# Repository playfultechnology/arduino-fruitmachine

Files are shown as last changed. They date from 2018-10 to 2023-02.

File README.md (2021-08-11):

# arduino-fruitmachine
This repository contains code listings, wiring diagrams, notes, and other reference information relating to my experiences of disassembling old (generally broken, sold as "for spares for repairs") fruit machines (or, "slot machines", for U.S. friends) into their various constituent components, and then rebuilding their functionality using an Arduino microprocessor as a controller.
Accompanying videos can be found at https://www.youtube.com/playlist?list=PLogiUurtMYtRenE8BooiE4FDIyxuIyZQj

As of July 2021, I have now followed this process with five different machines of different eras and manufacturers (Bell Fruit "Snakes and Ladders", Electrocoin "Magic 100", "Max-a-Million", Global "Tuppenny Nudger" and Global "Phoenix Knights"). Each machine has had different components, features, and designs, and I've tried to update the notes below to cover the different variations I've found.

<!-- ![Fruit Machine](FruitMachine.png?raw=true "Fruit Machine") -->
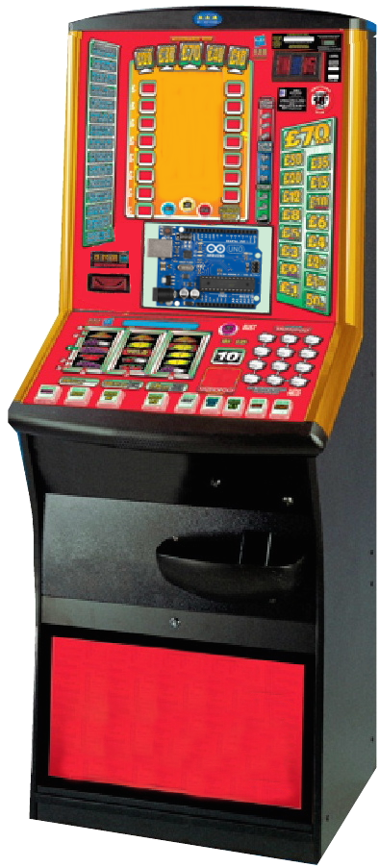
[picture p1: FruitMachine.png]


## Feature Reel
The feature reel is a single standalone reel, which makes it slightly easier to reverse-engineer than the main reels, which typically occur in a connected bank of three or four. It consists of a stepper motor, lamps, and an opto-sensor. Stepper motors may be 12V (in which they can be driven by a4988, DRV8825 stepper motor drivers of a CNC shield) or 24V (in which case they might need an L293D motor driver shield, as shown below)  
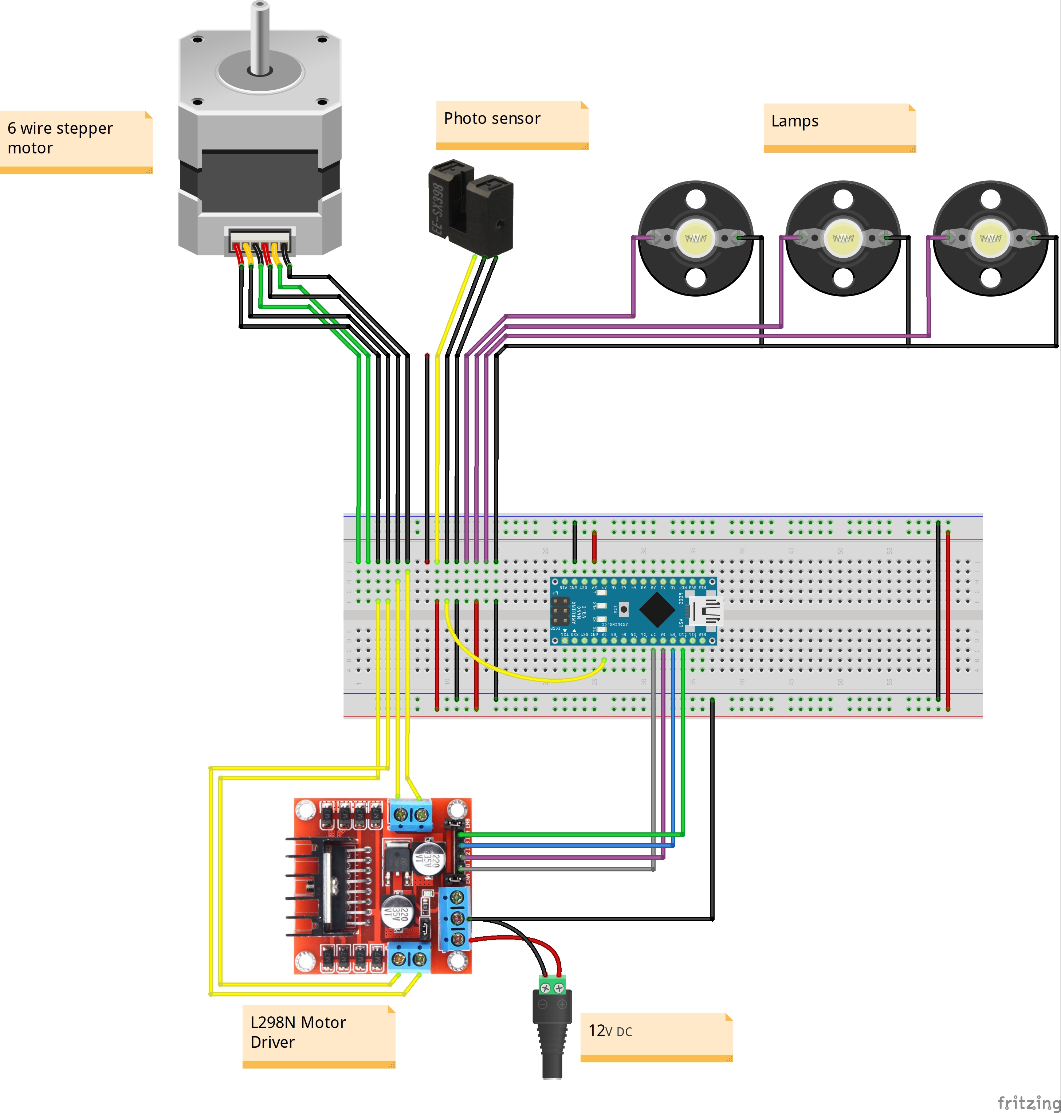
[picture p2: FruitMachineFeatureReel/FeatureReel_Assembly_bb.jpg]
Fruit Machine Feature Reel Fruit Machine Reel Assembly


## Reels
The reels work the same way as the feature reel, except that each has 16 positions, three lamps, and an opto-sensor. Rather than directly wire to a motor driver, I used a RAMPS shield, which provides a convenient way to interface with stepper motor drivers (A4988, DRV8825, TMC2209 or similar)
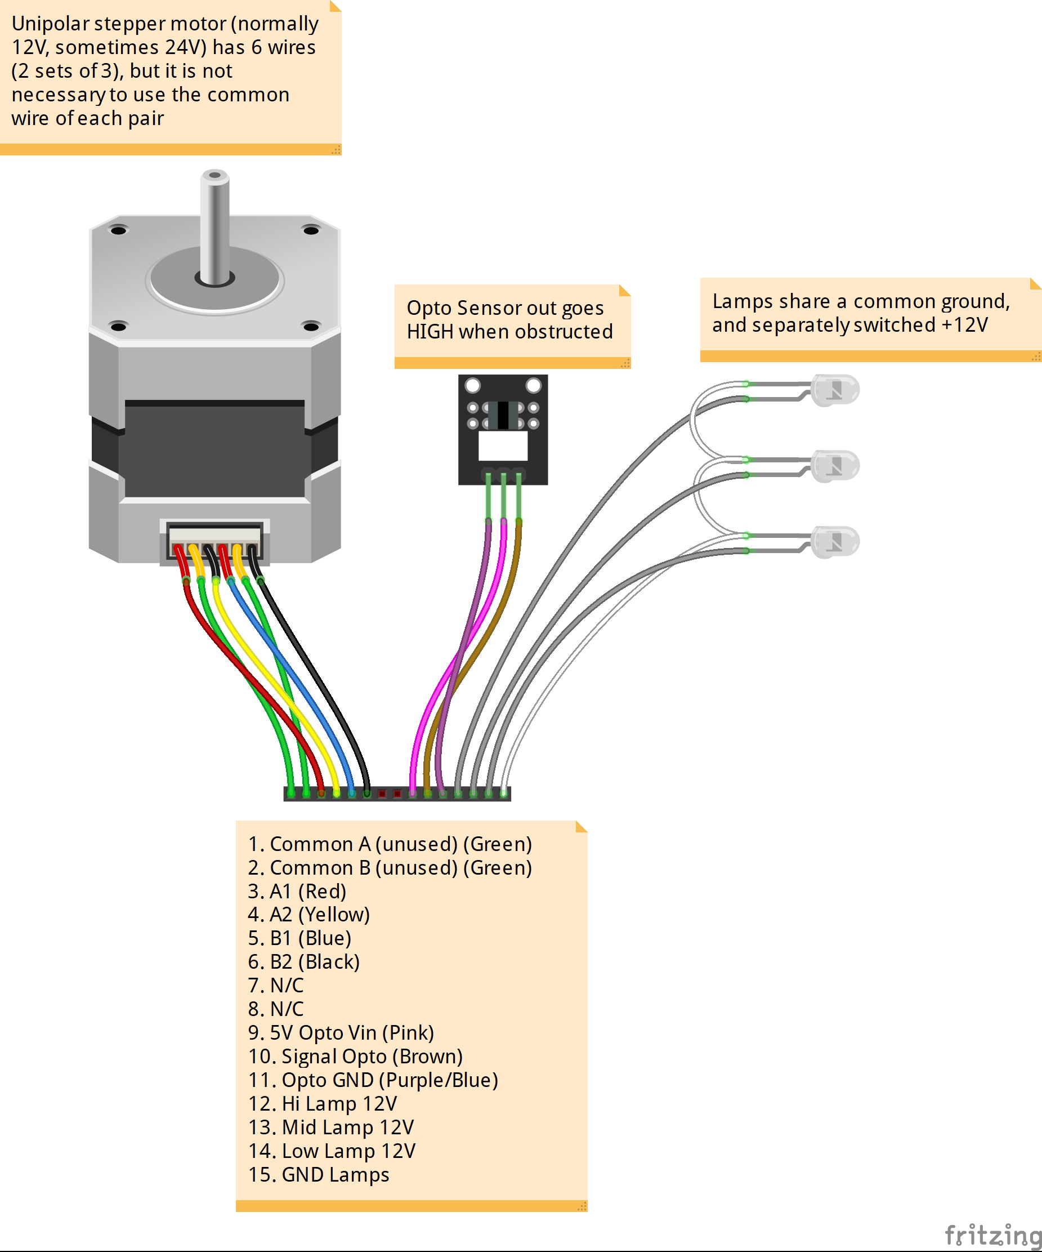
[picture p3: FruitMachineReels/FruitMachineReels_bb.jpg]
Fruit Machine Feature Reel Fruit Machine Reels


## Optosensors (A.K.A. Photosensors, Slotted Optical Switches etc.)
These are the little devices that are used to detect the position of the reels - they consist of a IR transmitter pointing at an IR receiver, with a small gap between them (~1cm). The reels have a small tab protuding from them at one point, which blocks the IR beam as it passes the gap in the sensor, making it possible to know the rotation of the reel at that point. I have encountered several variations of adaptor board which attach the opto-sensors to the reel assmebly, as follows:
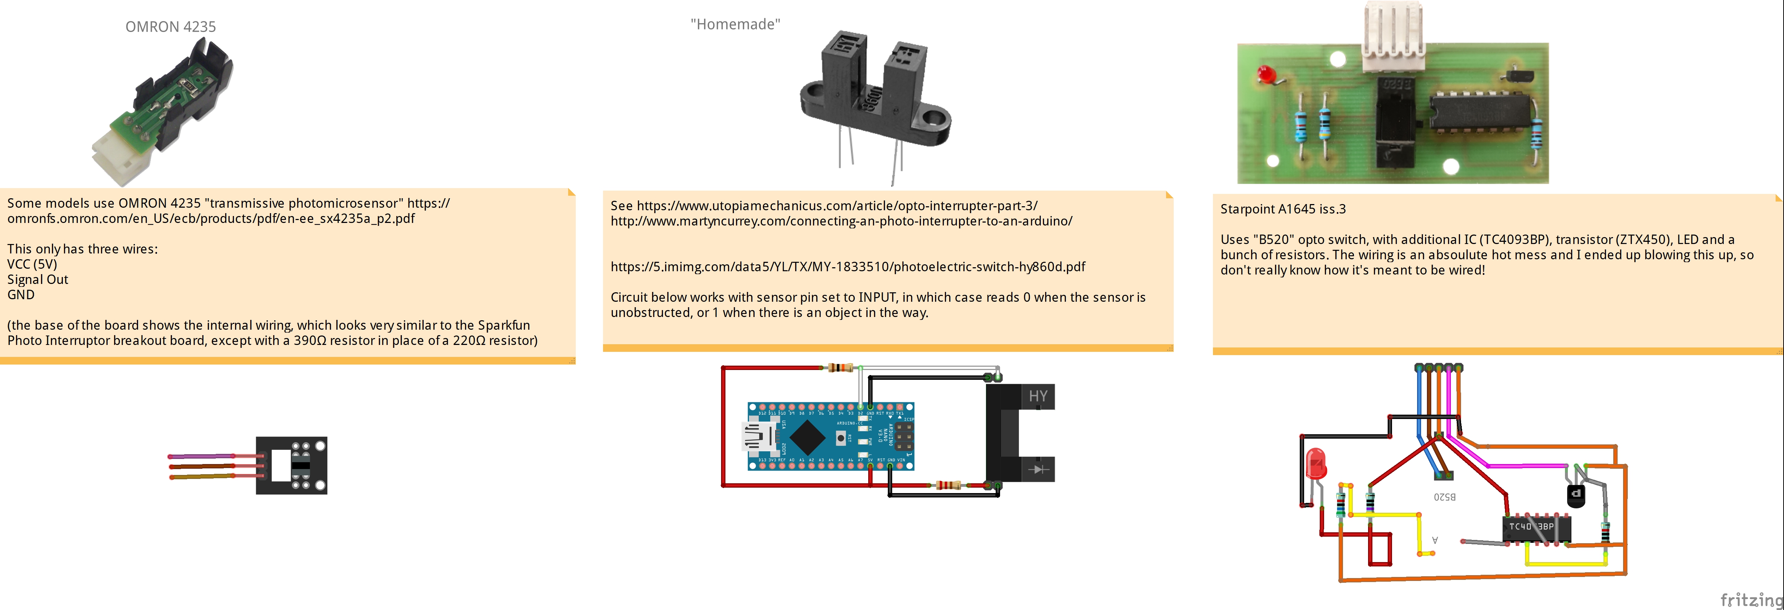
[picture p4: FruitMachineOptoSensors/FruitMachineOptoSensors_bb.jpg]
Fruit Machine Opto Sensors


## Hopper
There are two commonly-used interfaces for coin hoppers - serial and parallel. 
### Parallel interface
The parallel interface is easy to understand - the hopper simply dispenses coins as soon as, and far as long as, 24V power is connected. A coin counter output pin is connected to ground every time a coin exits the hopper, which can be used to cut power once sufficient coins have been dispensed.
### Serial interface
A serial interface called CCTalk was introduced to make universal communication standard with various monetary devices in machines - note validators, coin mechs, and hoppers. The CCTalk standard defines a set of messages that are sent over a serial connection (you can view the documentation here: http://www.coinoperatorshop.com/media/products/manual/cctalk/cctalk44-2.pdf).

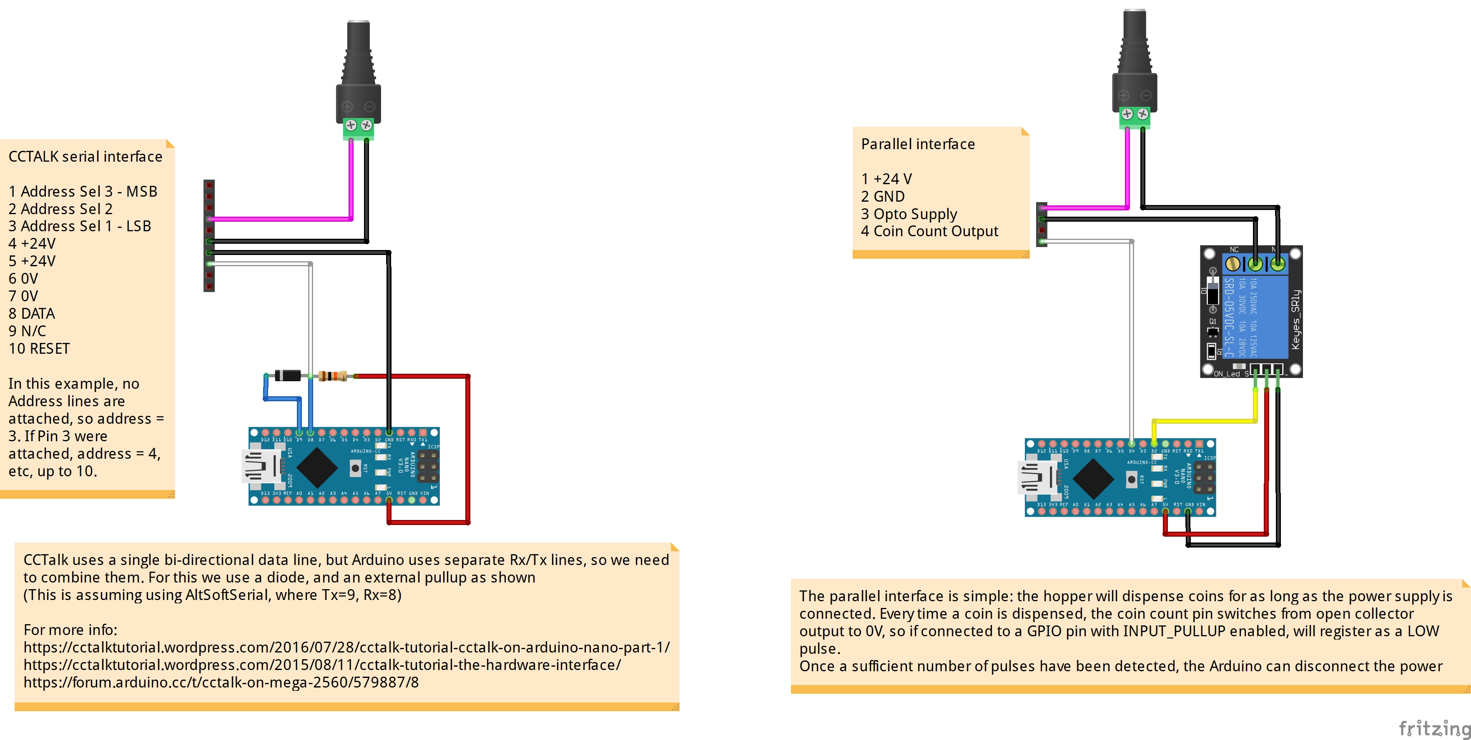
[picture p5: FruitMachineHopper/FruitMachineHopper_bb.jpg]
Fruit Machine Hopper


## LED Display
The primary LED display is formed from five interlocking 1.8" common cathode 7-segment LED displays - datasheet can be found at  http://www.farnell.com/datasheets/99300.pdf
To use the displays, I'm sourcing current into the anodes of each segment using a UDN2981 high-side darlington transistor array (the channels of the UDN2981, corresponding to the segments to be lit, are set by a 74HC595 shift register). The segments of all the displays are wired together, and the particular digit to be lit is selected by grounding the common cathode of that digit through a ULN2803 low-side darlington transistor array. The ULN2803 too is set by a 74HC595 which is daisy-chained to the first, meaning all 5 digit displays can be set using just three pins on the Arduino.

Update: 
 - the 74HC595+UDN2981 on the high side can be replaced with a single MIC5891 8-channel source driver
 - the 74HC595+ULN2803 on the low side can be replaced with a single TPIC6595 8-channel sink driver

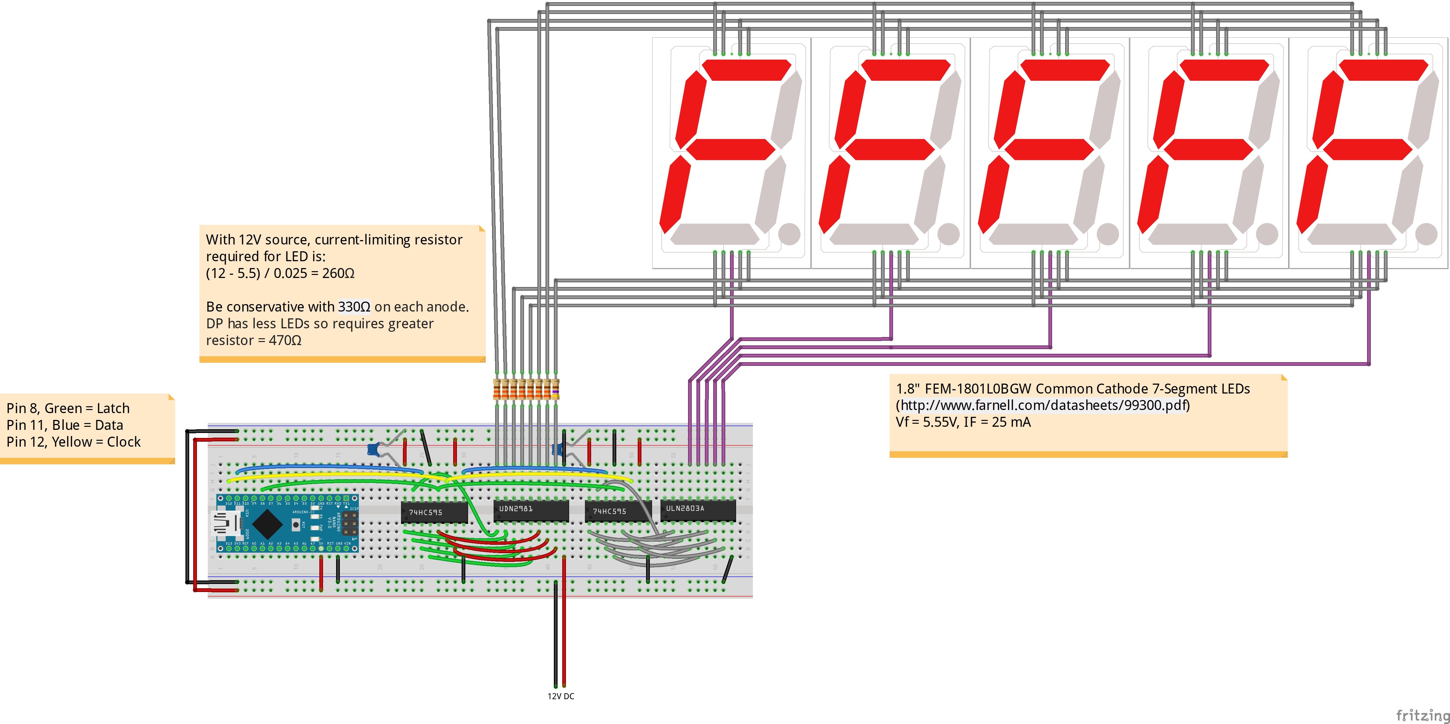
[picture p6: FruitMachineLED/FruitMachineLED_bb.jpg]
Fruit Machine LED Displays Fruit Machine LED Display


## VFD Display
https://picaxeforum.co.uk/threads/using-spi-serial-vfds-from-fruit-machines-with-picaxe-comprehensive-code-examples.22552/
https://www.fruitemu.co.uk/ib/index.php?app=forums&module=forums&controller=topic&id=17419

## Lamps
The incandescent lamps were arranged into groups around the machine, attached to long harnesses consisting of cable-tied wires, rather resembling a spinal column. 
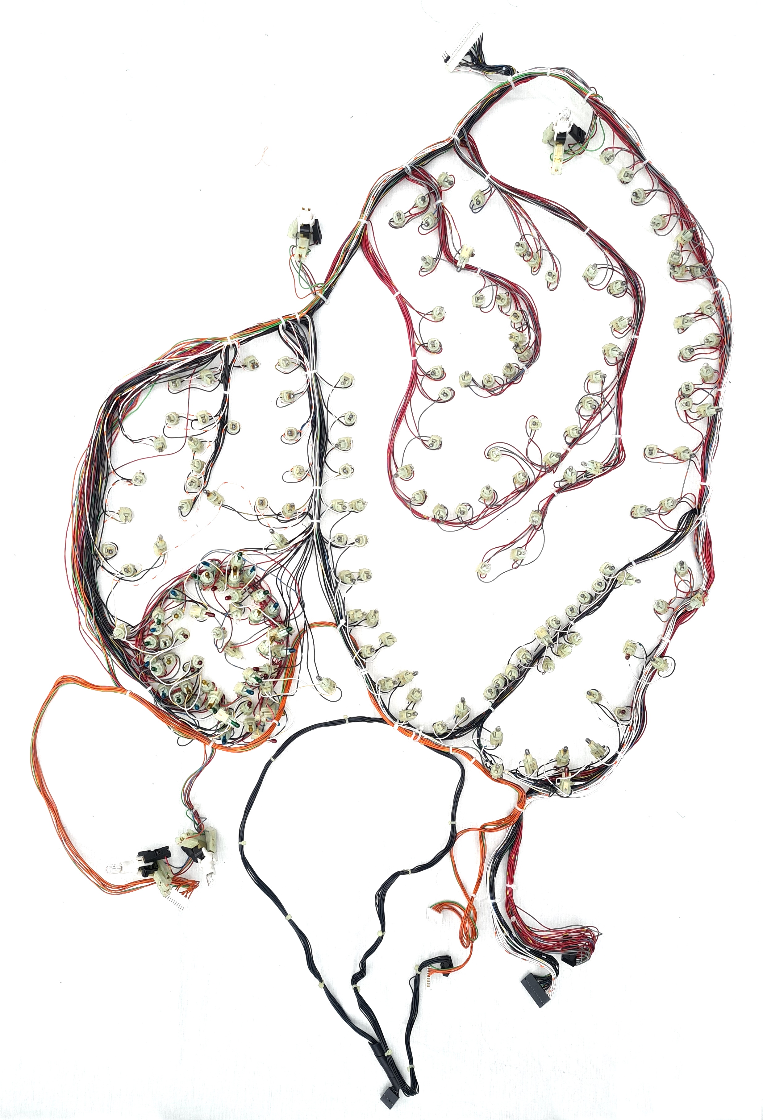
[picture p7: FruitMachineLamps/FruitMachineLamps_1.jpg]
Fruit Machine Lamp Wiring


Although the lamps themselves do not have polarity, the bulb holders typically have had a small inline diode inserted the housing, meaning they have a distinct "positive" and "negative" side. As such, wiring them is much the same as wiring 12V LEDs. Note that the colouring of the wires does not necessarily follow any standard convention: in the following photograph, note the line signifying the cathode of the diode shows the *red* wire is GND, while the *grey* wire is +12V.  
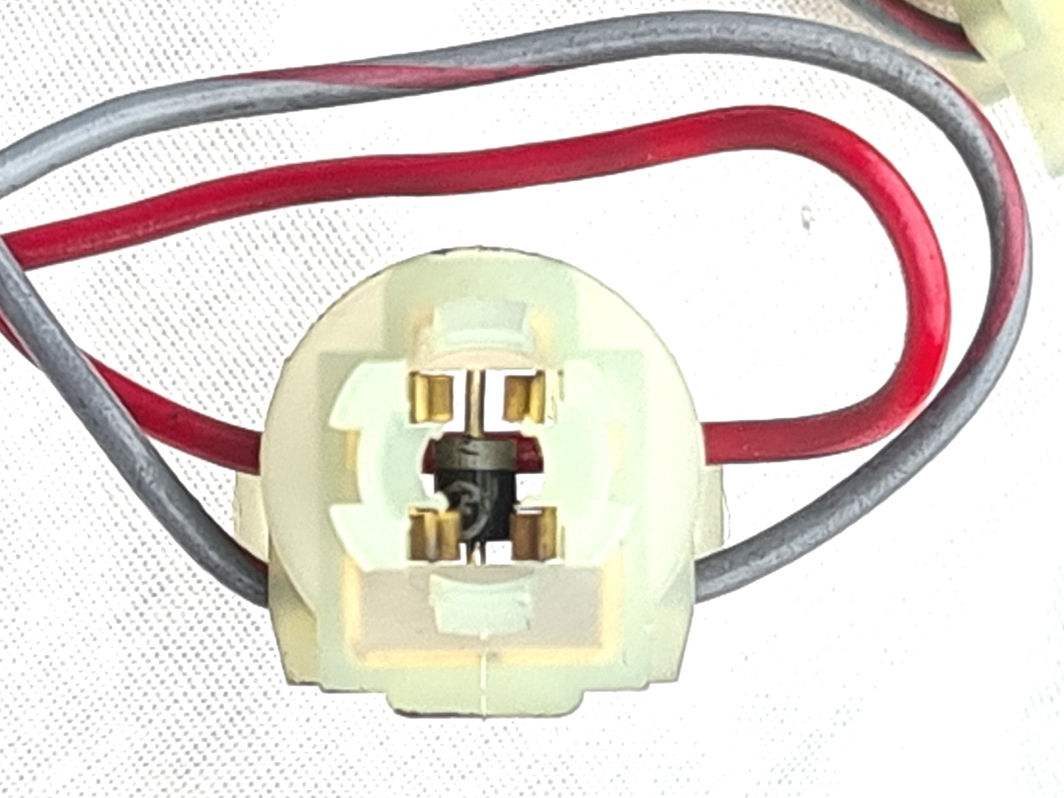
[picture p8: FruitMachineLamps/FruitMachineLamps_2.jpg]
Fruit Machine Lamp Wiring


In some machines, the lamps in a group all shared a common ground but each lamp has their own individual 12V wire ("high-side" switching). 
In other machines, the lamps share a common 12V supply, but each lamp has their own unique ground connection ("low-side" switching), as in the photograph below. 
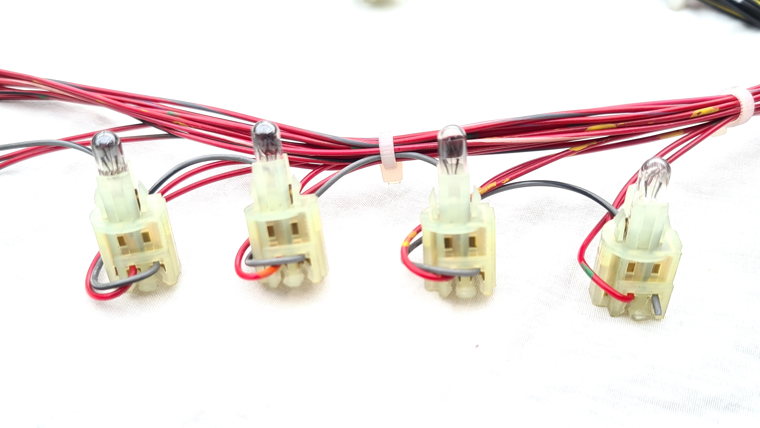
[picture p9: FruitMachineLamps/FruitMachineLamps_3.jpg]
Fruit Machine Lamp Wiring


The following circuits demonstrate how to wire a group of eight 12V lamps to be individually-switched using a power shift register - using a TPIC6B595 for low-side switching, or MIC5891 for high-side switching.
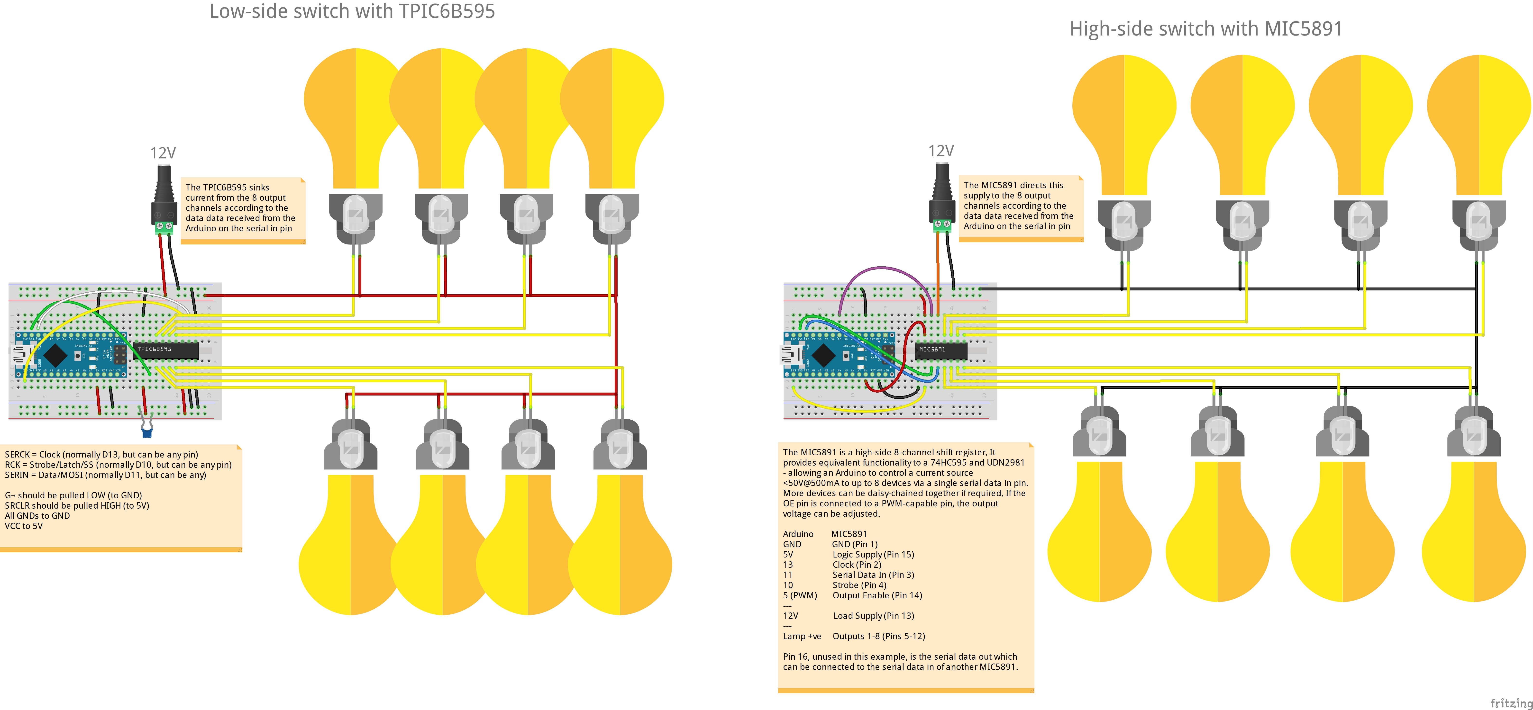
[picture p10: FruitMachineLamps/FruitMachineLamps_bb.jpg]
Fruit Machine Lamps


## Illuminated Buttons
The original buttons, like the lamps, were illuminated with individual 12V incandescent bulbs, sharing a common ground and individually switched 12V supply wires. To facilitate easier wiring and greater functionality, I decided to replace these with PL9823 LEDs. PL9823s are similar to common "Neopixel" or WS2812 LEDs, in that they are indiviudally-addressable, RGB LEDs, and any number of them can be chained together in a long series controlled by only a single data pin on an Arduino. However, unlike Neopixels which commonly come supplied on a strip, PL9823s are individual LEDs supplied in a 5mm form factor, just like a regular LED (except with 4 pins, not 2).
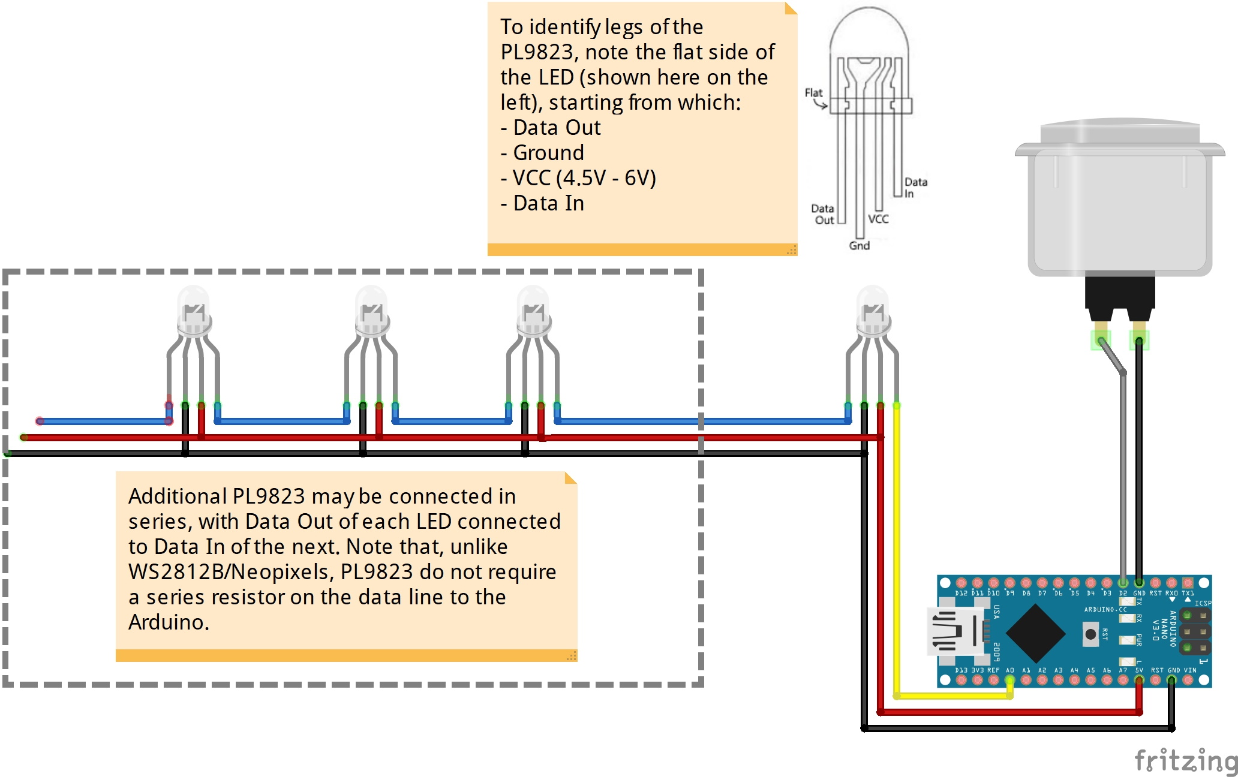
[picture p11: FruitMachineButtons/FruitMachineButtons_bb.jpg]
Illuminated Fruit Machine Buttons


## Counters
The counters are the most simple electronic components. 
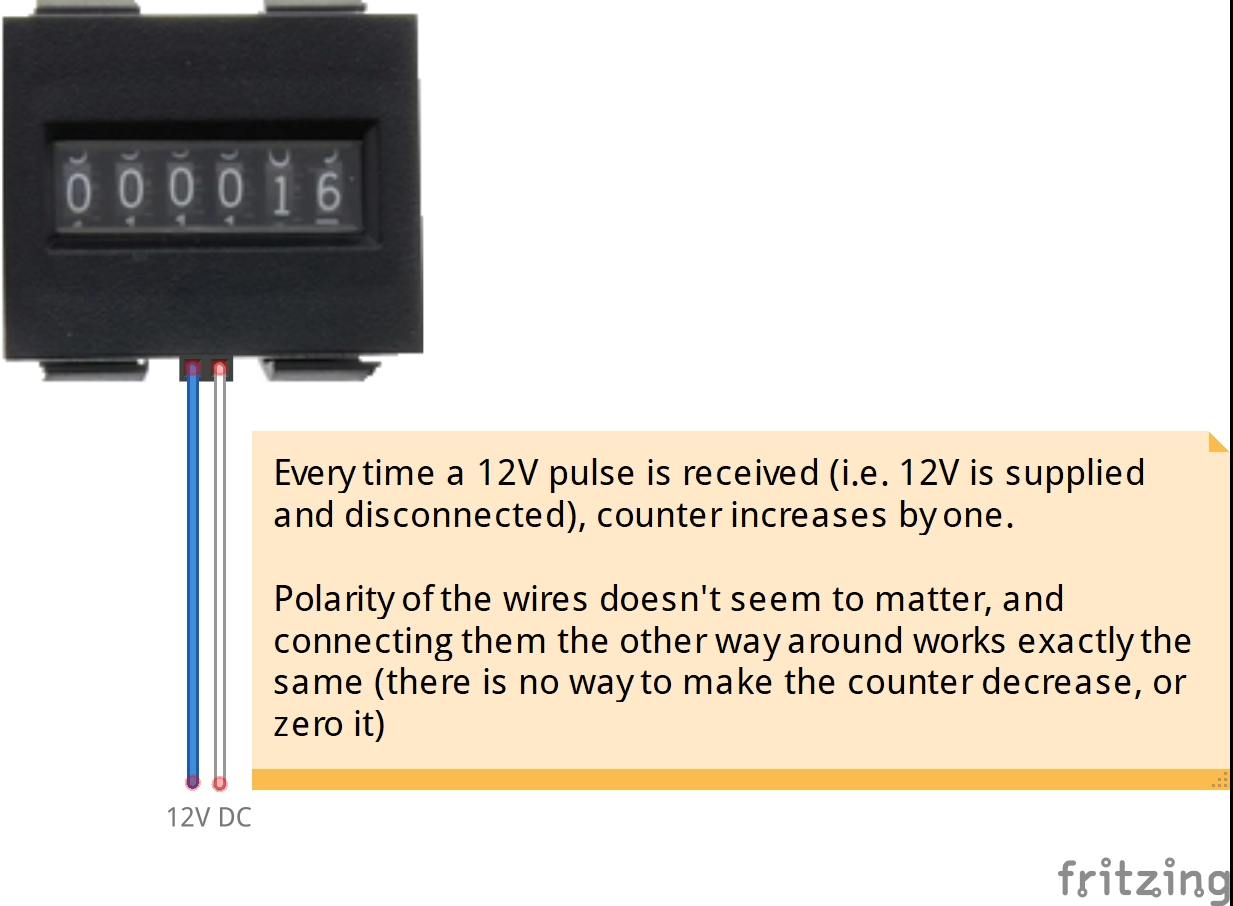
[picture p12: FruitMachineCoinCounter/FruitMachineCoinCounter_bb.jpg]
Counters Fruit Machine Coin Counter


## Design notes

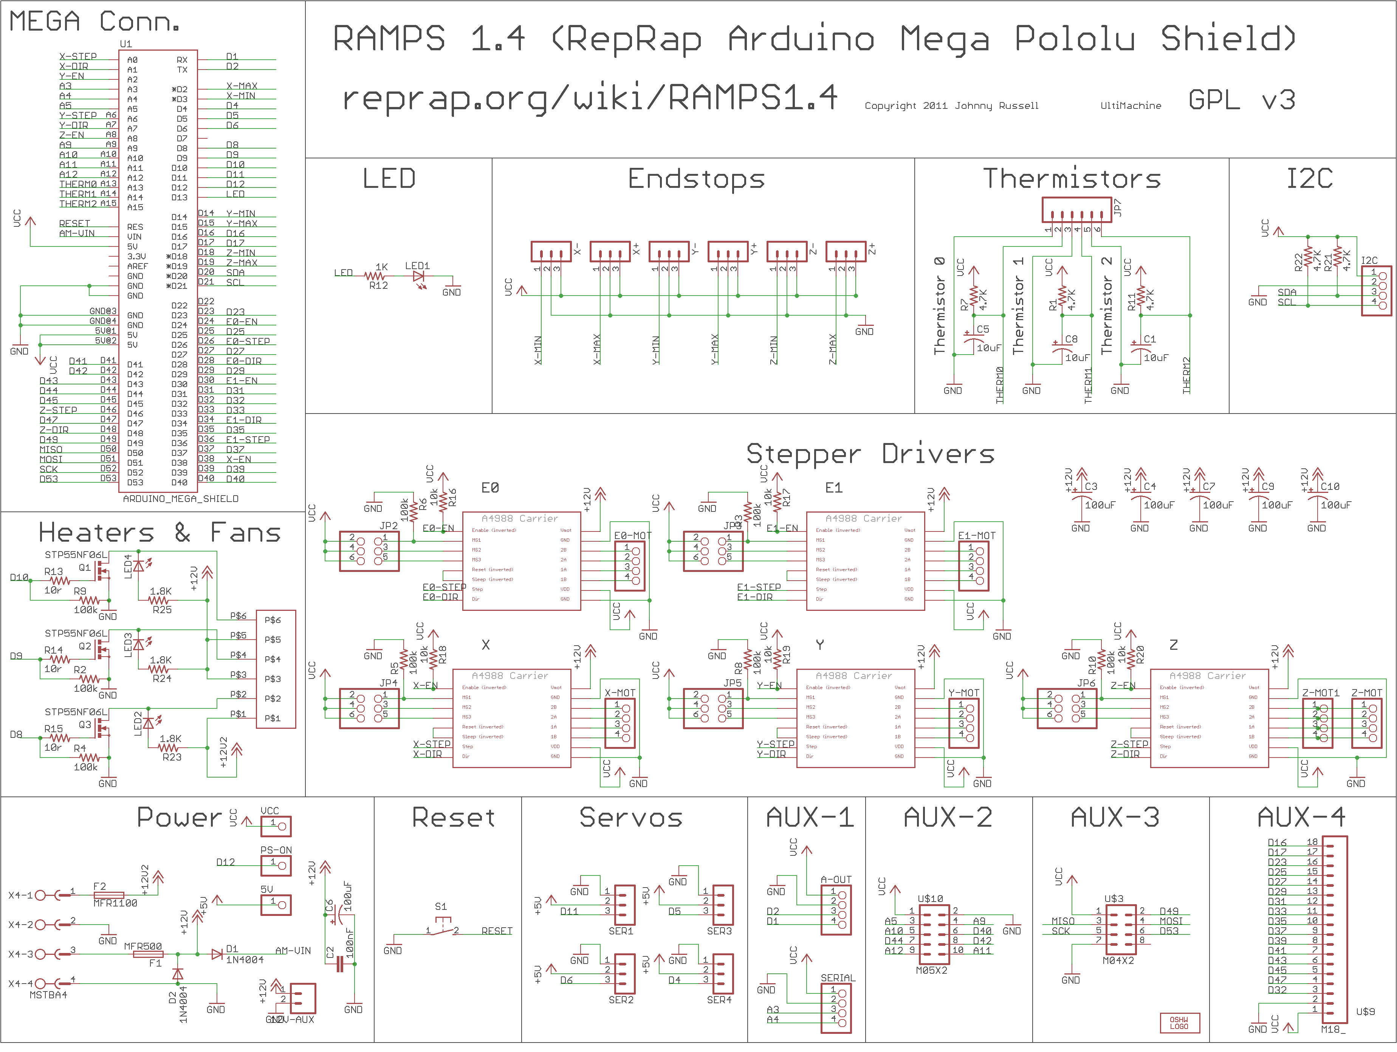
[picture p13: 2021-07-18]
Arduinomegapololushieldschematic.png

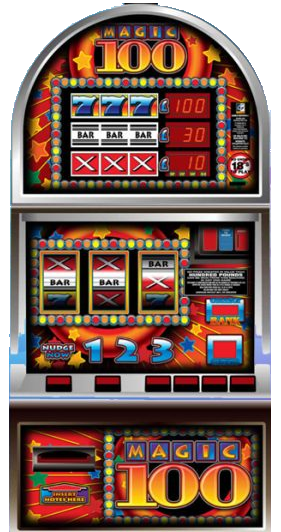
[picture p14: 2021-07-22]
Magic100.png

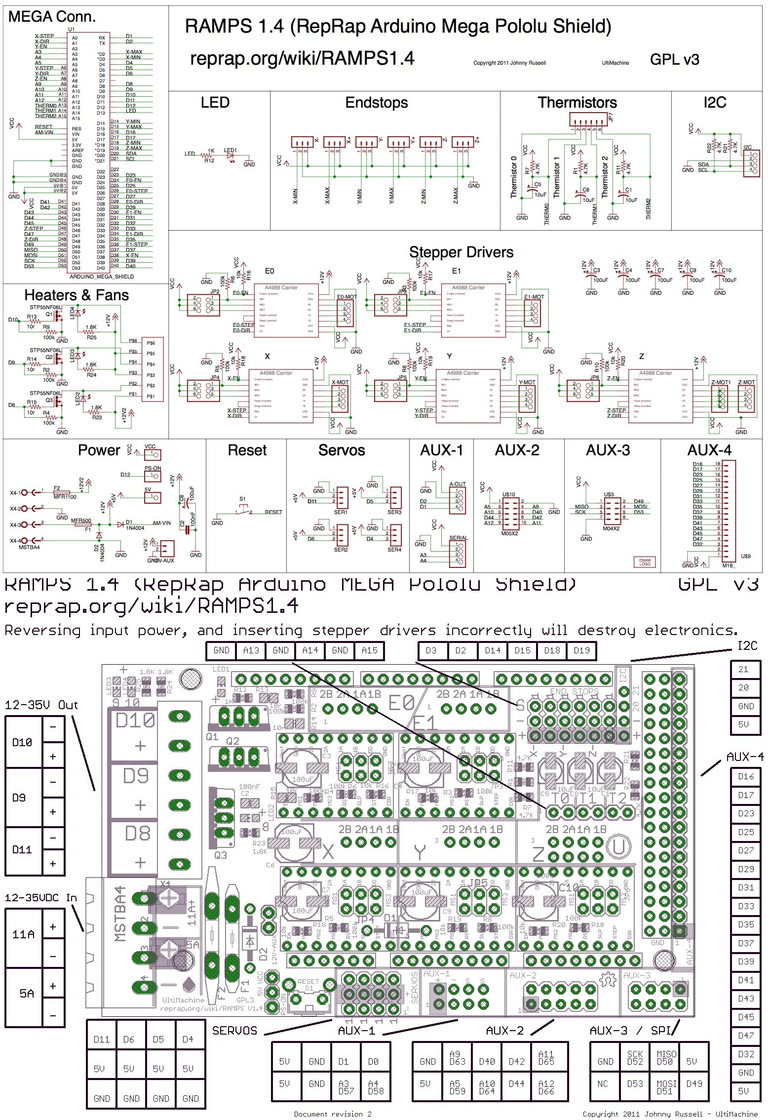
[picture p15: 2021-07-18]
34589604-dbd41b72-f16e-11e7-99a5-c91d116a0bd9.png

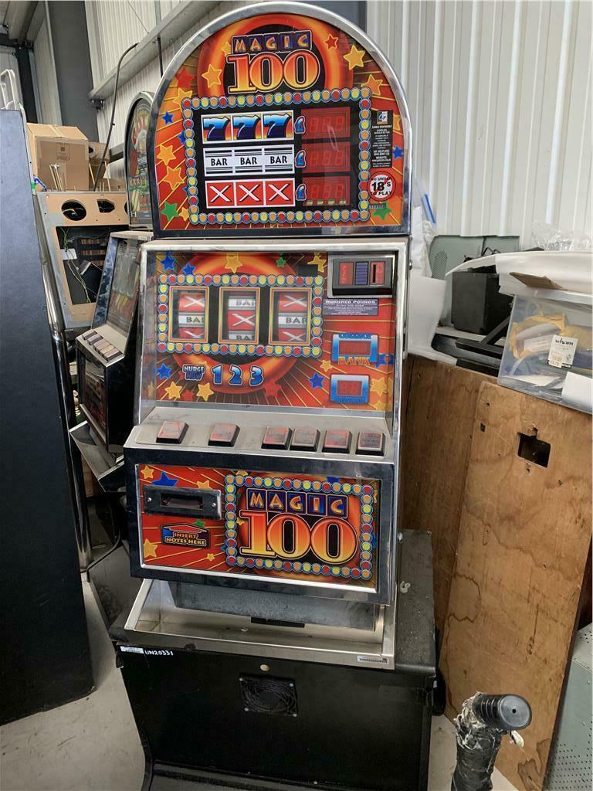
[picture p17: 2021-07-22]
Electrocoin-Magic-100-Fruit-Machine-£100-Jackpot.jpg

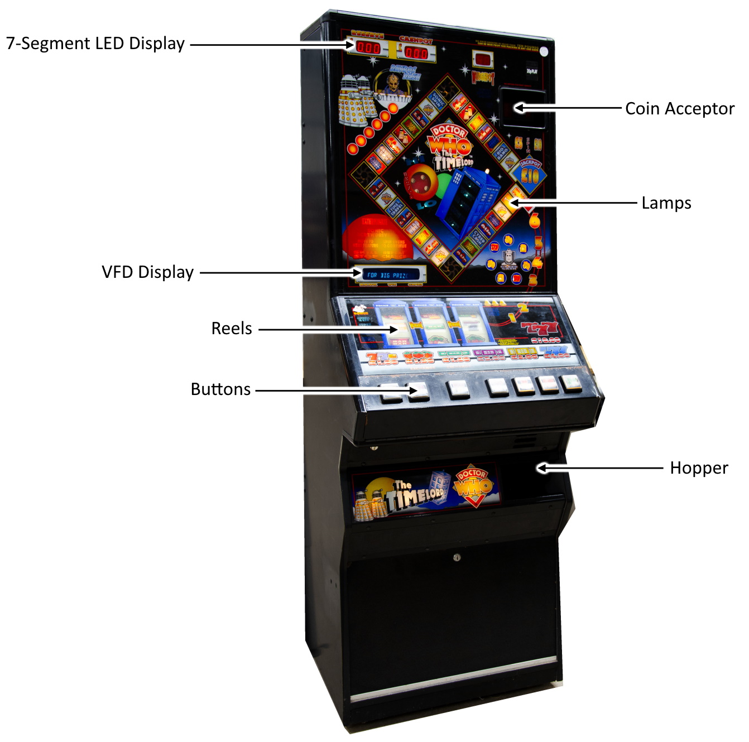
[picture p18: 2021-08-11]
labelled.jpg

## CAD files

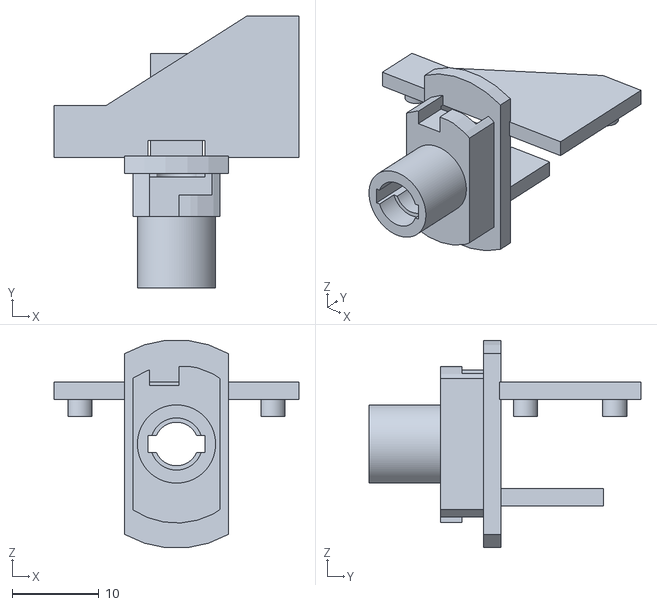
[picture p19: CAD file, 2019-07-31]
FruitMachineButtons/ArcadeButtonLEDHolder.stl
28.2 x 31.3 x 23.9

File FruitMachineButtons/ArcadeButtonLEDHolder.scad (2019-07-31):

ledHolderScrewType2();


module ledHolderScrewType2() {

difference() {
  union() {
      /*
      translate([22.2/2, -4, -10.3/2])
      rotate([90,0,0])
      #intersection() {
          cylinder(r=18/2, h=4);
          translate([-10/2, -18/2, 0])
            cube([10,18,12]);
        }
      */
      
    // Plate with clips
    linear_extrude(height=2)
      polygon(points = [[0-3,0-3],[22.2+3,-3],[22.2+3,10.3+3], [22.2-3,10.3+3], [3,3], [0-3,3]]);
    translate([-0,0,-2])
      cylinder(r=1.4, h=2.4, $fn=100);
    translate([22.2,10.3,-2])
      cylinder(r=1.4, h=2.4, $fn=100); 
    // Blank plate
    translate([22.2/2-3,-3,-10.3-2])
      cube([6,12,2]);
  }
  // Side channel for feeding wires to LED
  translate([22.2/2-3.3, -4, -10.3/2-1])
    cube([6.6,3,20]);
}
// Main block
difference() {
    
  union(){
    translate([22.2/2, -3, -10.3/2])
      rotate([90,0,0])
        intersection() {
          cylinder(r=18.2/2, h=6.8);
          translate([-10/2, -18.2/2, 0])
            cube([10,18,12]);
        }
        translate([22.2/2-6, -4.8, -10.3/2-14])
        intersection() {
            #cube([12,2,28]);
         rotate([90,0,0])
            translate([6, 14, -2])
        #cylinder(r=12, h=2);
        }
  }

  // Twist to secure channel
  #translate([11.5,-9.8,-14.3])
  rotate([0,0,0])
    linear_extrude(height=2.4)
    polygon(points = [[-.4,0],[3,0],[3,5],[-4.2,5], [-4.2,2.5], [-.4,2.5] ]);

  // Twist to secure other channel
  #translate([11,-9.8,4.0])
  rotate([0,180,0])
    linear_extrude(height=2.4)
    polygon(points = [[-.4,0],[3,0],[3,5],[-4.2,5], [-4.2,2.5], [-.4,2.5] ]);
  
  // Channel for LED legs
  translate([22.2/2, 10, -10.3/2])
    rotate([90,0,0])
      cylinder(r=2.5, h=20, $fn=100);
  
    translate([22.2/2-3.3, -31, -10.3/2-1])
      #cube([6.6,50,2]);
  
  
  // Side channel for feeding wires to LED
  translate([22.2/2-3.3, -5.2, -10.3/2])
    #cube([6.6,3,10.3/2+2]);
}    

// LED holder
difference() {
translate([22.2/2, -8, -10.3/2])
  rotate([90,0,0], $fn=100)
    cylinder(r=4.5, h=10);

  translate([22.2/2, -15.1, -10.3/2])
    rotate([90,0,0])
      #cylinder(r=3, h=10, $fn=100); 
  
  translate([22.2/2, 0, -10.3/2])
   rotate([90,0,0])
    cylinder(r=2.5, h=18, $fn=100);

  translate([22.2/2-3.3, -31, -10.3/2-1])
      #cube([6.6,50,2]);

}

}




module ledHolderScrewType() {

difference() {
  union() {
    // Plate with clips
    linear_extrude(height=2)
      polygon(points = [[0-3,0-3],[22.2+3,-3],[22.2+3,10.3+3], [22.2-3,10.3+3], [3,3], [0-3,3]]);
    translate([-0,0,-2])
      cylinder(r=1.4, h=2.4, $fn=100);
    translate([22.2,10.3,-2])
      cylinder(r=1.4, h=2.4, $fn=100); 
    // Blank plate
    translate([22.2/2-3,-3,-10.3-2])
      cube([6,12,2]);
  }
  // Channel for LED legs
  translate([22.2/2-2.8, -3, -10.3/2-1])
    #cube([5.6,2,20]);
}
// Main block
difference() {
    
  union(){
    translate([22.2/2, -3, -10.3/2])
      rotate([90,0,0])
        intersection() {
          cylinder(r=18/2, h=5.6);
          translate([-10/2, -18/2, 0])
            cube([10,18,12]);
        }
  }

  // Twist to secure channel
  translate([11.5,-8.6,-14.2])
  rotate([0,0,0])
    linear_extrude(height=2.4)
    polygon(points = [[0,0],[3,0],[3,4.8],[-4.2,4.8], [-4.2,3], [0,3] ]);

  // Twist to secure other channel
  translate([11,-8.6,3.9])
  rotate([0,180,0])
    linear_extrude(height=2.4)
    polygon(points = [[0,0],[3,0],[3,4.8],[-4.2,4.8], [-4.2,3], [0,3] ]);
  
  translate([22.2/2-2.8, -3, -10.3/2-2.8])
    #cube([5.6,4,24]);
  
  // Channel for LED legs
  translate([22.2/2, -5, -10.3/2])
    rotate([90,0,0])
      cylinder(r=2.5, h=20, $fn=100);
  
  
}    

// LED holder
difference() {
translate([22.2/2, -8, -10.3/2])
  rotate([90,0,0], $fn=100)
    cylinder(r=4.5, h=10);

  translate([22.2/2, -15.1, -10.3/2])
    rotate([90,0,0])
      cylinder(r=3, h=3, $fn=100); 
  
  translate([22.2/2, -8, -10.3/2])
   rotate([90,0,0])
    #cylinder(r=2.5, h=18, $fn=100);
      //#cube([5.6,50,2]);

}
}







module ledHolderPushType() {

// Plate with clips
linear_extrude(height=2)
  polygon(points = [[0-3,0-3],[22.2+3,-3],[22.2+3,10.3+3], [22.2-3,10.3+3], [3,3], [0-3,3]]);
translate([-0,0,-2])
  cylinder(r=1.4, h=2.4, $fn=100);
translate([22.2,10.3,-2])
  cylinder(r=1.4, h=2.4, $fn=100); 
// Blank plate
translate([22.2/2-3,-3,-10.3-2])
  cube([6,12,2]);




// Main block
difference() {
    
  union(){
    translate([22.2/2, -3, -10.3/2])
      rotate([90,0,0])
        intersection() {
          cylinder(r=18/2, h=10);
          translate([-10/2, -18/2, 0])
            cube([10,18,12]);
        }

    // Pins
    translate([22.2/2, -2.8 -8.6, -21/2-10.3/2])
      cylinder(r=2.1/2, h=21, $fn=100);
  }

  // Flex holes
  translate([22.2/2-6, -15, -.5])
    cube([12,10,2]);
  translate([22.2/2-6, -15, -11.9])
    cube([12,10,2]);
  
  // Side channel for LED legs
  translate([22.2/2-3.3, -7, -10.3/2])
  #cube([6.6,4,12]);
  
  // Central channel for LED legs
  translate([22.2/2-3.3, -25, -10.3/2-1])
    cube([6.6,50,2]);

  translate([22.2/2, 0, -10.3/2])
    rotate([90,0,0])
      #cylinder(r=2.5, h=30, $fn=100);   
  
}    

// LED holder
difference() {
translate([22.2/2, -12, -10.3/2])
  rotate([90,0,0], $fn=100)
    cylinder(r=4.5, h=16);

  translate([22.2/2, -25.1, -10.3/2])
    rotate([90,0,0])
      cylinder(r=3.5, h=3, $fn=100); 
  
  translate([22.2/2-3.3, -31, -10.3/2-1])
      cube([6.6,50,2]);

  translate([22.2/2, 0, -10.3/2])
    rotate([90,0,0])
      #cylinder(r=2.5, h=30, $fn=100);   
  

}
}

//translate([0,0,-10.3])
//v3_micro_switch(type = 1); // 1 = std switch, 2 = long roller, 3 = short roller, 4 = lever







//Outer module - sets parameters
module v3_micro_switch(type = 2)
{

if(type == 1) // 
{
	_micro_switch(
				ms_length= 22.2,
				ms_height = 10.3,
				ms_width = 10.3,
				ms_m_hole_rad = 3.1 / 2,
				ms_m_hole_offset = (3.4 - 3.1)/2,
				ms_outer_rad = 2.8,
				ms_switch_pos = 20.1,
				ms_switch_rad = 2,
				ms_switch_width = 4.2,
				ms_switch_length = 2.8,
				ms_switch_pt = 1.2,
				ms_switch_ot = 0.8,
				ms_open= true, // 0 = open or 1 = closed
				
				ms_term_width = 4.8,
				ms_term_length = 10,
				ms_term_thick = 0.6,
				ms_term_offset_1_y = 2.7,
				ms_term_offset_2_y = 0.7,
				ms_term_offset_3_y = 7,	

				ms_roller = false, 
				ms_roller_rad = 0,
				ms_roller_width = 0,
				ms_roller_offset = 0,
				ms_roller_length = 0,
				ms_roller_thick = 0,
				ms_roller_clip = 0
				
				
			);
}
if(type == 2) //long roller
{
	_micro_switch(
				ms_length= 22.2,
				ms_height = 10.3,
				ms_width = 10.3,
				ms_m_hole_rad = 3.1 / 2,
				ms_m_hole_offset = (3.4 - 3.1)/2,
				ms_outer_rad = 2.8,
				ms_switch_pos = 20.1,
				ms_switch_rad = 2,
				ms_switch_width = 4.2,
				ms_switch_length = 2.8,
				ms_switch_pt = 1.2,
				ms_switch_ot = 0.8,
				ms_open= true, // 0 = open or 1 = closed
				
				ms_term_width = 4.8,
				ms_term_length = 10,
				ms_term_thick = 0.6,
				ms_term_offset_1_y = 2.7,
				ms_term_offset_2_y = 0.7,
				ms_term_offset_3_y = 7,	

				ms_roller = true, 
				ms_roller_rad = 4.8 /2,
				ms_roller_width = 4.8,
				ms_roller_offset = 8.5,
				ms_roller_length = 34,
				ms_roller_thick = 0.6,
				ms_roller_clip = 2
				
				
			);
}
if(type == 3) //short roller
{
	_micro_switch(
				ms_length= 22.2,
				ms_height = 10.3,
				ms_width = 10.3,
				ms_m_hole_rad = 3.1 / 2,
				ms_m_hole_offset = (3.4 - 3.1)/2,
				ms_outer_rad = 2.8,
				ms_switch_pos = 20.1,
				ms_switch_rad = 2,
				ms_switch_width = 4.2,
				ms_switch_length = 2.8,
				ms_switch_pt = 1.2,
				ms_switch_ot = 0.8,
				ms_open= true, // 0 = open or 1 = closed
				
				ms_term_width = 4.8,
				ms_term_length = 10,
				ms_term_thick = 0.6,
				ms_term_offset_1_y = 2.7,
				ms_term_offset_2_y = 0.7,
				ms_term_offset_3_y = 7,	

				ms_roller = true, 
				ms_roller_rad = 4.8 /2,
				ms_roller_width = 4.8,
				ms_roller_offset = 8.5,
				ms_roller_length = 20.1,
				ms_roller_thick = 0.6,
				ms_roller_clip = 2
				
				
			);
}

if(type == 4)//lever
{
	_micro_switch(
				ms_length= 22.2,
				ms_height = 10.3,
				ms_width = 10.3,
				ms_m_hole_rad = 3.1 / 2,
				ms_m_hole_offset = (3.4 - 3.1)/2,
				ms_outer_rad = 2.8,
				ms_switch_pos = 20.1,
				ms_switch_rad = 2,
				ms_switch_width = 4.2,
				ms_switch_length = 2.8,
				ms_switch_pt = 1.2,
				ms_switch_ot = 0.8,
				ms_open= true, // 0 = open or 1 = closed
				
				ms_term_width = 4.8,
				ms_term_length = 10,
				ms_term_thick = 0.6,
				ms_term_offset_1_y = 2.7,
				ms_term_offset_2_y = 0.7,
				ms_term_offset_3_y = 7,	

				ms_roller = true, 
				ms_roller_rad =0,
				ms_roller_width = 4.8,
				ms_roller_offset = 8.5,
				ms_roller_length = 60,
				ms_roller_thick = 0.6,
				ms_roller_clip =0
				
				
			);
}

}
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

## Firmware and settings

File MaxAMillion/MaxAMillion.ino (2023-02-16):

/**
   Arduino "Max-A-Million" Fruit Machine Controller
   Copyright (c) 2021 Playful Technology
*/

// INCLUDES
#include "src/common.h"
// https://github.com/thomasfredericks/Bounce2
#include <Bounce2.h>
// See: http://www.airspayce.com/mikem/arduino/AccelStepper/
#include <AccelStepper.h>
// For interfacing with MP3 sound board
#include "SerialMP3Player.h"
// For starburst VFD display
#include "src/Samsung_16LF01_VFD.h"
// I2C connection to 7-segment daughterboard
#include <Wire.h>

// DEFINES
// The total number of steps required for one complete revolution of the reel motor
#define NUM_STEPS 48 // - 7.5° step angle = 48 steps
// Number of steps between adjacent symbols on the reel
#define STEPS_PER_VALUE 4 // - i.e. NUM_STEPS / Number of Symbols
// RAMPS Pin definitions from https://github.com/MarlinFirmware/Marlin/blob/2.0.x/Marlin/src/pins/ramps/pins_RAMPS.h
#define X_STEP_PIN         54
#define X_DIR_PIN          55
#define X_ENABLE_PIN       38
#define X_MIN_PIN           3
#define X_MAX_PIN           2
#define Y_STEP_PIN         60
#define Y_DIR_PIN          61
#define Y_ENABLE_PIN       56
#define Y_MIN_PIN          14
#define Y_MAX_PIN          15
#define Z_STEP_PIN         46
#define Z_DIR_PIN          48
#define Z_ENABLE_PIN       62
#define Z_MIN_PIN          18
#define Z_MAX_PIN          19
#define E_STEP_PIN         26
#define E_DIR_PIN          28
#define E_ENABLE_PIN       24
#define Q_STEP_PIN         36
#define Q_DIR_PIN          34
#define Q_ENABLE_PIN       30
#define LED_PIN            13
#define PS_ON_PIN          12
// Note Pin D8 is wired to the separate 11A power supply and does not share any power with the rest of the board
#define HEATER_1_PIN       8
// Pins D9 and D10 share the main 5A power supply. They are "common anode", in that the +ve terminals are connected
// together, and are switched on only by grounding the separate -ve terminals.
#define FAN_PIN            9
#define HEATER_0_PIN       10
#define NO_SERIALMP3_DELAY

// CONSTANTS
const byte numReels = 4;
const byte numSymbolsPerReel = 12;
// Use the X/Y min/max end stop pins to wire the opto sensors
const byte optoSensorPins[numReels] = {X_MIN_PIN, X_MAX_PIN, Y_MIN_PIN, Y_MAX_PIN};
const byte stepperEnablePins[numReels] = {X_ENABLE_PIN, Y_ENABLE_PIN, Z_ENABLE_PIN, E_ENABLE_PIN};
// The max speed at which each stepper will turn (in steps/sec)
const int stepperSpeeds[numReels] = {60, 20, 18, 16};
// Inputs are connected to GPIO pins on the AUX-2 board
const byte numButtons = 7;
// Buttons connected to these pins, from L-R: 1:Cancel, 2:Hold, 3:Hold, 4:Hold, 5:Hold, 6:Auto, 7:Start/Gamble
const byte buttonPins[numButtons] = {63, 59, 40, 64, 42, 44, 65};
// Button connected to opto-sensor to detect coin insertion
const byte coinPin = 66;
// VFD Starburst Display connected to AUX-3 connector
const byte VFDClockPin = 51;
const byte VFDResetPin = 52;
const byte VFDDataPin = 50;
// Delay (in ms) at which VFD display scrolls
const uint16_t vfdScrollDelay = 200;
// RC input channels connected to Servos connector
const byte numRCs = 4;
const byte RCinputPins[numRCs] = {11, 6, 5, 4};
// Relay outputs connected to lower AUX-4 pins
const byte numRelays = 8;
// 8-channel relay supplies 12VDC power to 0:Glass lamps, 1:Reel lamps, 2:Gamble Button lamp, 3-5:Hold Button Lamps, 7:Maglock release
const byte relayOutPins[numRelays] = {35, 37, 39, 41, 43, 45, 47, 32};
// Define the combination of relays that are on/off for each of the states: Initialising, AwaitingCoin, Ready, Spinning
const byte relayStateInitialising = 0b00000000;
const byte relayStateAwaitingCoin = 0b00000000;
const byte relayStateReady = 0b11100000;
const byte relayStateSpinning = 0b11011100;
// I2C address of daughterboard that will control 7-segment LED display
const byte slave7SegmentAddress = 9;
// Define all the possible symbols that appear on the reels
enum Symbols {Diamond, Double, Treble, Zero, One, Three, Five, Max, Hat, Jackpot};
const char* SymbolNames[] = {"Diamond", "Double", "Treble", "Zero", "One", "Three", "Five", "Max", "Hat", "Jackpot"};
// The pattern of symbols as they appear on each reel
const byte ReelSymbols[numReels][numSymbolsPerReel] = {
  {Diamond, Double, Diamond, Double, Diamond, Treble, Diamond, Double, Diamond, Treble, Diamond, Double},
  {Max, Three, One, Jackpot, Hat, Five, One, Hat, Three, One, Five, One},
  {Hat, Zero, Zero, Jackpot, Hat, Zero, Hat, Zero, Zero, Jackpot, Max, Zero},
  {Max, Hat, Zero, Jackpot, Hat, Zero, Zero, Max, Zero, Hat, Zero, Zero}
};

// GLOBALS
// Define each stepper and the pins it will use
AccelStepper stepperX(AccelStepper::DRIVER, X_STEP_PIN, X_DIR_PIN);
AccelStepper stepperY(AccelStepper::DRIVER, Y_STEP_PIN, Y_DIR_PIN);
AccelStepper stepperZ(AccelStepper::DRIVER, Z_STEP_PIN, Z_DIR_PIN);
AccelStepper stepperE(AccelStepper::DRIVER, E_STEP_PIN, E_DIR_PIN);
AccelStepper steppers[4] = {stepperX, stepperY, stepperZ, stepperE};
// VFD display
Samsung_16LF01_VFD vfd(VFDClockPin, VFDDataPin, VFDResetPin);
// Used to keep track of when the VFD was last scrolled
unsigned long vfdTimer = 0;
// The complete message to be displayed
char message[64] = "                                                               ";
// The characters currently displayed on the VFD
char digits[17] = "                ";
int firstDigit = 0;
int lastDigit = strlen(message) - 1;
// Array of Bounce objects to help read each time a reel tab spins past the opto-sensor
Bounce optoSensors[numReels] = {};
Bounce buttons[numButtons] = {};
Bounce RCinputs[numRCs] = {};
Bounce coinSensor;
// Audio player
SerialMP3Player mp3;
// Overall game state
enum GameState {Initialising, AwaitingCoin, Ready, Spinning};
GameState gameState = GameState::Initialising;

// Initial setup
void setup() {
  // Start a serial connection
  Serial.begin(115200);
  // Don't wait for ages for serial input
  Serial.setTimeout(50);
  Serial.println(__FILE__ __DATE__);

  // Pause while we wait for all components to power up
  delay(1000);

  // Loop over every reel
  for (int i = 0; i < numReels; i++) {

    // Stepper drivers need to be enabled by pulling the EN pin low.
    // On some shields, the pin is automatically pulled to GND via a jumper. If not, write a LOW signal to
    // whatever pin is connected to the enable pin of the chip.
    pinMode(stepperEnablePins[i], OUTPUT);
    digitalWrite(stepperEnablePins[i], LOW);

    // Set the optosensor pins as inputs and attach pullups and debounce objects to them
    optoSensors[i].attach(optoSensorPins[i], INPUT_PULLUP);

    // AccelStepper speed is express in steps/sec
    // So, for a reel with NUM_STEPS 48, setMaxSpeed(60), means (60*60/48)= 75RPM
    steppers[i].setMaxSpeed(stepperSpeeds[i]);
    steppers[i].setAcceleration(250);
  }
  // Initialise input buttons
  for (int i = 0; i < numButtons; i++) {
    buttons[i].attach(buttonPins[i], INPUT_PULLUP);
  }
  coinSensor.attach(coinPin, INPUT_PULLUP);
  // Initialise RC inputs
  for (int i = 0; i < numRCs; i++) {
    RCinputs[i].attach(RCinputPins[i], INPUT_PULLUP);
  }
  for (int i = 0; i < numRelays; i++) {
    pinMode(relayOutPins[i], OUTPUT);
    digitalWrite(relayOutPins[i], HIGH);
  }

  // Join I2C bus (address optional for master)
  Wire.begin();

  // MP3 player is connected to pins 18/19, A.K.A. ZMin/ZMax, A.K.A. Serial1
  Serial1.begin(9600);
  mp3.begin(Serial1);
  mp3.sendCommand(CMD_SEL_DEV, 0, 2);   // Select SD-card as storage device

  // Initialize the VFD display (number of digits to use, brightness (in 1/31ths))
  vfd.begin (16, 25);
  // Display a welcome static message
  vfd.print("Clued Up!");
  delay(1000);
  vfd.clear();
  // Reset cursor to the first digit
  vfd.setCursor(0);
  // Display a welcome static message
  vfd.print("Calibrating...");
  delay(1000);
  vfd.clear();
  // Reset cursor to the first digit
  vfd.setCursor(0);

  // Calibrate reels to determine "zero" point
  CalibrateReels();

  // Setup complete - advance to the next state
  TransitionToAwaitingCoinState();
}

/**
   Reset procedure as described in 20RM_MK2_STI manual

   I. Drive the motor at approximately 50RPM.
   II. At every motor step change, monitor the optic output. Immediately the tab is detected by the optic cease driving the motor.
   III. Wait 500mS then power up the motor on the Black and Yellow windings. (Black and Yellow are the A windings of both coils)
   IV. Wait 500mS, this allows the motor/reel band to settle in position. Check the tab is in the optic.
       If not repeat steps i] to iv], if the tab is still not in the optic there is a fault.
   V. The reel mechanism and software are now initialised.
*/
void CalibrateReels() {
  Serial.println(F("Calibrating Reels"));

  for (int i = 0; i < numReels; i++) {

    // Enable the driver
    digitalWrite(stepperEnablePins[i], LOW);

    // Store the current max speed
    float maxSpeed = steppers[i].maxSpeed();

    // Set the stepper to a slower speed for calibration if desired
    // Manual suggests calibrating at 50RPM
    steppers[i].setMaxSpeed(50.0F / 60.0F * NUM_STEPS);

    // Set a target point several rotations away from the current position
    steppers[i].move(NUM_STEPS * 4);

    // numTriggers is the number of times the reel tab crosses the opto-sensor
    int numTriggers = 0;

    // Process until we reach the target
    while (steppers[i].distanceToGo() != 0) {
      steppers[i].run();
      optoSensors[i].update();
      // Most opto-sensors go HIGH when an obstruction is detected
      if (optoSensors[i].rose()) {
        // Increase the counter
        numTriggers++;
      }
      // When the tab crosses through the sensor for the third time
      if (numTriggers > 2) {
        // Set current position to zero
        steppers[i].setCurrentPosition(0);
        // (following lines are unnecessary as setCurrentPosition instantaneously sets speed to 0 anyway.
        //steppers[i].setSpeed(0);
        //steppers[i].stop();
        nonBlockingDelay(200);
        break;
      }
    }
    if (numTriggers <= 1) {
      logMessage(F("Calibration failed"));
    }

    // Now that calibration is complete, restore the normal max motor speed
    steppers[i].setMaxSpeed(maxSpeed);

    // Disable motor driver to conserve power
    // digitalWrite(stepperEnablePins[i], HIGH);

    // Play a sound effect
    mp3.play(i + 1);

    // Slight pause before calibrating next motor
    nonBlockingDelay(100); // was delay()
  }
  Serial.println(F("Calibration complete"));
}

void UpdateVFD() {
  unsigned long now = millis();
  if (now - vfdTimer > vfdScrollDelay) {
    // Move all the chars in the array one to the left
    for (int i = 0; i < 15; i++) {
      digits[i] = digits[i + 1];
    }
    // Place the next new digit in the rightmost character slot
    digits[15] = message[firstDigit];
    // Increment the counter (and loop back if we get to the end of the message)
    if (firstDigit == lastDigit) {
      firstDigit = 0;
    }
    else {
      firstDigit = firstDigit + 1;
    }

    // Now actually update the display with the new values in the char array
    for (int i = 0; i < 16; i++) {
      vfd.print(digits[i]);
      // Workaround, "points" and "commas" are in the same digit
      if (digits[i] == ',' || digits[i] == '.') {
        vfd.print(" ");
      }
    }
    vfdTimer = now;
  }
}

void TransitionToAwaitingCoinState() {
  vfd.clear();
  vfd.setCursor(0);
  strcpy(message, "Welcome to Clued Up casino! Insert one quarter to play!        ");
  // Set the lamps on for this state
  for (int i = 0; i < 8; i++) {
    // bitRead is LSB (i.e. reads bits from the right-hand side), so we subtract from 7 to make line up with relay order
    digitalWrite(relayOutPins[i], bitRead(relayStateInitialising, 7 - i) == 1 ? LOW : HIGH);
  }
  gameState = GameState::AwaitingCoin;
}

void TransitionToReadyState() {
  // Update the display
  vfd.clear();
  vfd.setCursor(0);
  strcpy(message, "Spin the reels! Get three Jackpots to win a prize!             ");
  // Play one-shot sound effect
  mp3.play(17);
  // Set the lamps for this state
  for (int i = 0; i < 8; i++) {
    // bitRead is LSB (i.e. reads bits from the right-hand side), so we subtract from 7 to make line up with relay order
    digitalWrite(relayOutPins[i], bitRead(relayStateReady, 7 - i) == 1 ? LOW : HIGH);
  }
  gameState = GameState::Ready;
}

void TransitionToSpinningState() {
  // Use playSL to loop music
  mp3.playSL(18);
  // Set the lamps for this state
  for (int i = 0; i < 8; i++) {
    // bitRead is LSB (i.e. reads bits from the right-hand side), so we subtract from 7 to make line up with relay order
    digitalWrite(relayOutPins[i], bitRead(relayStateSpinning, 7 - i) == 1 ? LOW : HIGH);
  }
  // Calculate targets for all but the leftmost reel (the multiplier reel, which we don't use)
  for (int i = 1; i < numReels; i++) {
    digitalWrite(stepperEnablePins[i], LOW);
    // Calculate *absolute* position that is next multiple of whole number of revolutions
    long target = roundUp(steppers[i].currentPosition(), NUM_STEPS);
    // Then add on a further number of whole revolutions
    target += NUM_STEPS * 20;
    // moveTo is absolute
    steppers[i].moveTo(target);
  }
  gameState = GameState::Spinning;
}

// The accelstepper run() function *must* be called continuously (even when you don't think the steppers have anything to do)
// so that means using the regular delay() function is a no-no.
// This alternative method performs no program logic, but continues to execute the stepper updates for the specified
// amount of time and is used in place of delay()
void nonBlockingDelay(unsigned long wait) {
  unsigned long waitUntil = millis() + wait;
  while (millis() < waitUntil) {
    for (int i = 0; i < numReels; i++) {
      steppers[i].run();
    }
  }
}

void loop() {
  // INPUTS
  // Opto-sensors
  for (int i = 0; i < numReels; i++) {
    optoSensors[i].update();
  }
  // Buttons
  for (int i = 0; i < numButtons; i++) {
    buttons[i].update();
  }
  // RC buttons
  for (int i = 0; i < numRCs; i++) {
    RCinputs[i].update();
  }
  // Coin sensor
  coinSensor.update();

  // "A" button on RC
  if (RCinputs[0].fell()) {
    logMessage(F("RC Channel 0 pressed"));
    // Start/stop countdown timer
    Wire.beginTransmission(slave7SegmentAddress);
    Wire.write(0x00);
    Wire.endTransmission();
  }
  // "B" button on RC
  else if (RCinputs[1].fell()) {
    logMessage(F("RC Channel 1 pressed"));
    // Reset the countdown timer
    Wire.beginTransmission(slave7SegmentAddress);
    Wire.write(0x01);
    Wire.endTransmission();
  }
  // "C" button on RC
  else if (RCinputs[2].fell()) {
    logMessage(F("RC Channel 2 pressed"));
    // Solve the puzzle
    for (int i = 0; i < numReels; i++) {

      // Enable the driver
      digitalWrite(stepperEnablePins[i], LOW);

      // Store the current max speed
      float maxSpeed = steppers[i].maxSpeed();

      // Set the stepper to a slower speed for calibration if desired
      // Manual suggests calibrating at 50RPM
      steppers[i].setMaxSpeed(50.0F / 60.0F * NUM_STEPS);

      // Set a target point several rotations away from the current position
      steppers[i].move(NUM_STEPS * 4);

      // Process until we reach the target
      while (steppers[i].distanceToGo() != 0) {
        steppers[i].run();
        optoSensors[i].update();
        // Most opto-sensors go HIGH when an obstruction is detected
        if (optoSensors[i].rose()) {
          // Set current position to zero
          steppers[i].setCurrentPosition(0);
          // (following lines are unnecessary as setCurrentPosition instantaneously sets speed to 0 anyway.
          //steppers[i].setSpeed(0);
          //steppers[i].stop();
          steppers[i].moveTo(3 * STEPS_PER_VALUE);
        }
      }

      // Now that calibration is complete, restore the normal max motor speed
      steppers[i].setMaxSpeed(maxSpeed);

      // Disable motor driver to conserve power
      // digitalWrite(stepperEnablePins[i], HIGH);

      // Play a sound effect
      mp3.play(i + 1);

      // Slight pause before calibrating next motor
      nonBlockingDelay(100); // was delay()
    }

    Serial.println("WINNNNNNNERRRRRR!!!!");
    // Display a message
    vfd.clear();
    // Reset cursor to the first digit
    vfd.setCursor(0);
    vfd.print("WINNNERRRRR!!!");
    // Play the "Winner" sound effect
    mp3.play(20);
    // Release maglock here
    digitalWrite(relayOutPins[7], LOW);
    nonBlockingDelay(500);
    digitalWrite(relayOutPins[7], HIGH);
    nonBlockingDelay(500);
    // Reset state
    TransitionToAwaitingCoinState();
  }
  // "D" button on RC
  else if (RCinputs[3].fell()) {
    logMessage(F("RC Channel 3 pressed"));
    CalibrateReels();
  }

  // Update the VFD display by scrolling the current message
  UpdateVFD();

  // Rest of behaviour depends on the current state of the game
  switch (gameState) {

    case GameState::Initialising:
      TransitionToAwaitingCoinState();
      break;

    case GameState::AwaitingCoin:
      if (coinSensor.fell()) {
        logMessage(F("Coin inserted"));
        TransitionToReadyState();
      }
      break;

    case GameState::Ready:
      // Cancel
      if (buttons[0].fell()) { ; }
      // Start/Gamble
      if (buttons[6].fell()) {
        logMessage(F("Button 6 pressed"));
        TransitionToSpinningState();
      }
      break;

    case GameState::Spinning:
      if (buttons[2].fell()) {
        logMessage(F("Button 2 pressed"));
        // Turn off this hold button lamp
        digitalWrite(relayOutPins[3], HIGH);
        // This code will stop the reel immediately
        //steppers[1].setSpeed(0);
        //steppers[1].stop();
        // This code will stop the reel at the next symbol
        long target = roundUp(steppers[1].currentPosition(), STEPS_PER_VALUE);
        // moveTo is absolute
        steppers[1].moveTo(target);
        // Increase speed of other motors
        //steppers[2].setMaxSpeed(steppers[2].maxSpeed() + 20);
        //steppers[3].setMaxSpeed(steppers[3].maxSpeed() + 20);

      }
      if (buttons[3].fell()) {
        logMessage(F("Button 3 pressed"));
        // Turn off this hold button lamp
        digitalWrite(relayOutPins[4], HIGH);
        //steppers[2].setSpeed(0);
        //steppers[2].stop();
        long target = roundUp(steppers[2].currentPosition(), STEPS_PER_VALUE);
        // moveTo is absolute
        steppers[2].moveTo(target);
        // Increase speed of other motors
        //steppers[1].setMaxSpeed(steppers[1].maxSpeed() + 20);
        //steppers[3].setMaxSpeed(steppers[3].maxSpeed() + 20);
      }
      if (buttons[4].fell()) {
        logMessage(F("Button 4 pressed"));
        // Turn off this hold button lamp
        digitalWrite(relayOutPins[5], HIGH);
        // steppers[3].setSpeed(0);
        // steppers[3].stop();
        long target = roundUp(steppers[3].currentPosition(), STEPS_PER_VALUE);
        // moveTo is absolute
        steppers[3].moveTo(target);
        // Increase speed of other motors
        //steppers[1].setMaxSpeed(steppers[1].maxSpeed() + 20);
        //steppers[2].setMaxSpeed(steppers[2].maxSpeed() + 20);
      }

      bool allReelsStopped = true;
      // This gets called every frame, and processes any movement of the steppers as necessary
      for (int i = 0; i < numReels; i++) {
        steppers[i].run();
        if (steppers[i].isRunning()) {
          allReelsStopped = false;
        }
      }
      if (allReelsStopped) {
        mp3.stop();
        bool winningLine = true;
        for (int i = 1; i < numReels; i++) {
          // Work out what symbol each reel is showing
          byte symbolPos = (steppers[i].currentPosition() % NUM_STEPS) / STEPS_PER_VALUE;
          byte symbol = ReelSymbols[i][symbolPos];
          // DEBUG ONLY - Print the values on which the steppers stopped
          Serial.print(steppers[i].currentPosition() % NUM_STEPS);
          Serial.print(" (");
          Serial.print(SymbolNames[symbol]);
          Serial.print(")");
          if (i < numReels - 1) {
            Serial.print(",");
          }
          // If any reel is not showing the jackpot, it's not a winning line
          if (symbol != Jackpot) {
            winningLine = false;
          }
        }

        // Win!
        if (winningLine) {
          Serial.println("WINNNNNNNERRRRRR!!!!");
          // Display a message
          vfd.clear();
          vfd.setCursor(0);
          vfd.print("WINNNERRRRR!!!");
          // Play the "Winner" one-shot sound effect
          mp3.play(20);
          // Release maglock here
          digitalWrite(relayOutPins[7], LOW);
          nonBlockingDelay(500);
          digitalWrite(relayOutPins[7], HIGH);
          nonBlockingDelay(500);
          // Reset state
          TransitionToAwaitingCoinState();
        }
        // Fail!
        else {
          // Let them play again
          TransitionToReadyState();
        }
      }
      break;
  }
}

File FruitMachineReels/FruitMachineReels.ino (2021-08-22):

/**
 * Arduino Fruit Machine Reel Controller
 * Copyright (c) 2021 Playful Technology
 */
// DEFINES
// Helper function to get length of an arbitrary array
#define ArrayLength(x) (sizeof(x) / sizeof((x)[0]))

// The total number of steps required for one complete revolution of the reel motor
// Common values for motors are: 
// - 7.5° step angle = 48 steps
// - 1.8° step angle = 200 steps
#define NUM_STEPS 48

// STEPS_PER_VALUE is the number of steps between adjacent symbols on the reel
// Calculated as NUM_STEPS / (Number of Symbols)
// For 16 values on a 7.5° step angle reel (48 steps), STEPS_PER_VALUE 3 etc.
// For 12 values on a 7.5° step angle reel (48 steps), STEPS_PER_VALUE 4 etc.
// For 20 values on a  1.8° step angle reel (200 steps), STEPS_PER_VALUE 10 etc.
#define STEPS_PER_VALUE 4

// What sort of shield is being used to wire the components to the Arduino? 
// #define USE_CNCSHIELD (UNO) or #define USE_RAMPS (Mega)
#define USE_CNCSHIELD

// Pin definitions for Arduino MEGA with RAMPS v1.4 shield
// See https://github.com/MarlinFirmware/Marlin/blob/2.0.x/Marlin/src/pins/ramps/pins_RAMPS.h
#ifdef USE_RAMPS
  #define X_STEP_PIN         54
  #define X_DIR_PIN          55
  #define X_ENABLE_PIN       38
  #define X_MIN_PIN           3
  #define X_MAX_PIN           2
  #define Y_STEP_PIN         60
  #define Y_DIR_PIN          61
  #define Y_ENABLE_PIN       56
  #define Y_MIN_PIN          14
  #define Y_MAX_PIN          15
  #define Z_STEP_PIN         46
  #define Z_DIR_PIN          48
  #define Z_ENABLE_PIN       62
  #define Z_MIN_PIN          18
  #define Z_MAX_PIN          19
  #define E_STEP_PIN         26
  #define E_DIR_PIN          28
  #define E_ENABLE_PIN       24
  #define Q_STEP_PIN         36
  #define Q_DIR_PIN          34
  #define Q_ENABLE_PIN       30
  #define SDPOWER            -1
  #define SDSS               53
  #define LED_PIN            13
  #define PS_ON_PIN          12
  //#define KILL_PIN           -1
  // Note Pin D8 is wired to the separate 11A power supply and does not share any power with the rest of the board
  #define HEATER_1_PIN       8
  // Pins D9 and D10 share the main 5A power supply. They are "common anode", in that the +ve terminals are connected 
  // together, and are switched on only by grounding the separate -ve terminals.
  #define FAN_PIN            9
  #define HEATER_0_PIN       10  
  #define TEMP_0_PIN         13   // ANALOG NUMBERING
  #define TEMP_1_PIN         14   // ANALOG NUMBERING
  #define KILL_PIN 41 //[RAMPS14-SMART-ADAPTER]  
  #define LCD_PINS_RS 16 //[RAMPS14-SMART-ADAPTER]  
  #define LCD_PINS_ENABLE 17 //[RAMPS14-SMART-ADAPTER]  
  #define LCD_PINS_D4 23 //[RAMPS14-SMART-ADAPTER]  
  #define LCD_PINS_D5 25 //[RAMPS14-SMART-ADAPTER]  
  #define LCD_PINS_D6 27 //[RAMPS14-SMART-ADAPTER]  
  #define LCD_PINS_D7 29 //[RAMPS14-SMART-ADAPTER]  
  #define BTN_EN1 31 //[RAMPS14-SMART-ADAPTER]  
  #define BTN_EN2 33 //[RAMPS14-SMART-ADAPTER]  
  #define BTN_ENC 35 //[RAMPS14-SMART-ADAPTER]  
  #define BEEPER 37 //[RAMPS14-SMART-ADAPTER] / 37 = enabled; -1 = disabled / (if you don't like the beep sound ;-)
  #define SDCARDDETECT 49 //[RAMPS14-SMART-ADAPTER]  
#endif
// Pin definitions for Arduino UNO with CNC Shield v3
// see https://wiki.keyestudio.com/Ks0160_keyestudio_CNC_Shield_V3
// see https://blog.protoneer.co.nz/arduino-cnc-shield-v3-00-assembly-guide/
#ifdef USE_CNCSHIELD
  #define X_STEP_PIN          2
  #define X_DIR_PIN           5
  #define X_ENABLE_PIN        8 // Note all drivers are connected to same enable line
  #define X_MIN_PIN           9
  #define X_MAX_PIN           9 
  #define Y_STEP_PIN          3
  #define Y_DIR_PIN           6
  #define Y_ENABLE_PIN        8 // Note all drivers are connected to same enable line
  #define Y_MIN_PIN          10  
  #define Y_MAX_PIN          10  
  #define Z_STEP_PIN          4
  #define Z_DIR_PIN           7
  #define Z_ENABLE_PIN        8 // Note all drivers are connected to same enable line
  #define Z_MIN_PIN          11 
  #define Z_MAX_PIN          11  
  #define E_STEP_PIN         12 // Assumes jumper has been placed on board
  #define E_DIR_PIN          13 // Assumes jumper has been placed on board
  #define E_ENABLE_PIN        8 // Note all drivers are connected to same enable line
  #define LED_PIN            13
  #define SPN_EN_PIN         12 // Not usable if A has been attached   
  #define SPN_DIR            13 // Not usable if A has been attached
  #define COOL_EN_PIN        A3   
  #define ABORT_PIN          A0  
  #define HOLD_PIN           A1
  #define RESUME_PIN         A2
#endif

// CONSTANTS
const byte numReels = 1;

#ifdef USE_RAMPS
  // Use the X/Y min/max end stop pins to wire the opto sensors
  const byte sensorPins[4] = {X_MIN_PIN, X_MAX_PIN, Y_MIN_PIN, Y_MAX_PIN};
#elif defined(USE_CNCSHIELD)
  // The CNC shield only supports 3 endstops, so if we have >3 reels need to use another pin for the extra optosensors 
  const byte sensorPins[4] = {X_MIN_PIN, Y_MIN_PIN, Z_MIN_PIN, HOLD_PIN};
#endif

// INCLUDES
// See: http://www.airspayce.com/mikem/arduino/AccelStepper/
#include <AccelStepper.h>
// https://github.com/thomasfredericks/Bounce2
#include <Bounce2.h>
// 20x04 character LCD display
#include <LiquidCrystal.h>
// Rotary encoder
#include <Encoder.h>

// GLOBALS
// Define each stepper and the pins it will use
AccelStepper stepperX(AccelStepper::DRIVER, X_STEP_PIN, X_DIR_PIN);
AccelStepper stepperY(AccelStepper::DRIVER, Y_STEP_PIN, Y_DIR_PIN);
AccelStepper stepperZ(AccelStepper::DRIVER, Z_STEP_PIN, Z_DIR_PIN);
AccelStepper stepperE(AccelStepper::DRIVER, E_STEP_PIN, E_DIR_PIN);
//AccelStepper stepperQ(AccelStepper::DRIVER, Q_STEP_PIN, Q_DIR_PIN);
AccelStepper steppers[4] = {stepperX, stepperY, stepperZ, stepperE};
// Array of Bounce objects to help read each time a reel tab spins past the opto-sensor
Bounce optoSensors[4] = {};
// Initialize the LCD with specified interface pins
#ifdef USE_RAMPS
  LiquidCrystal lcd(LCD_PINS_RS, LCD_PINS_ENABLE, LCD_PINS_D4, LCD_PINS_D5, LCD_PINS_D6, LCD_PINS_D7);
#endif
// Create a char array to store the contents of the LCD screen
char displayBuffer[4][20];
// Encoder object
#ifdef USE_RAMPS
  Encoder encoder(BTN_EN2, BTN_EN1);
  long lastEncoderPosition  = -999;
  long currentEncoderPosition;
  // encButton is when encoder button (LS1) is pushed in
  Bounce2::Button encButton = Bounce2::Button();
  // button is the small black button (K1)
  Bounce2::Button button = Bounce2::Button();
#endif

/**
 * Copies the current contents of the display buffer to the LCD
 */
void updateDisplay() {
  #ifdef USE_RAMPS
  for(int i=0; i<4; i++) {
    lcd.setCursor(0,i);
    lcd.print(displayBuffer[i]);
  }
  #endif
}
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

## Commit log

2018-12-14 Reorganised directory structure
    [HC74595 and UDN2981 FruitMachine LED.fzz]
2018-12-19 Updated to use 74HC595s on both ULN2803 and UDN2981
    [FruitMachineLED.fzz]
2019-07-24 Update README.md
    Include alternative monolithic components to replace shift register + drivers on both high side and low side.
2019-07-31 Upload lamps wiring
    [FruitMachineLamps.fzz]
2019-07-31 FruitMachineButton diagram
    [FruitMachineButtons.fzz]
2019-07-31 Added illuminated buttons
2019-07-31 Added OpenSCAD and STL model for LED Holder
    [ArcadeButtonLEDHolder.scad, ArcadeButtonLEDHolder.stl]
2021-07-04 Updates reels to use RAMPS shield
    [FruitMachineReels.fzz]
2021-07-05 Added coincounter and hopper
    [FruitMachineCoinCounter.fzz]
2021-07-06 Added coin hopper
    [FruitMachineHopper.fzz]
2021-07-08 Lotsa updates
    [FruitMachineLED.fzz, FruitMachineLamps.fzz, FruitMachineOptoSensors.fzz]
2021-07-09 Added opto-sensors
    [FruitMachineOptoSensors.fzz]
2021-07-11 multiple updates to reels
    [FruitMachineReels.fzz]
2021-07-18 Upload RAMPS schematics
2021-07-19 Multiple updates
    [FruitMachineCoinCounter.fzz, FruitMachineCounter.fzz, FruitMachineLED.fzz]
2021-07-28 Updating the Reels code and wiring
    [FruitMachineReels.fzz]
2021-07-29 Added photographs of stepper harness wiring
2021-07-30 updated wiring
    [FruitMachine.fzz, FruitMachineLED.fzz]
2021-08-02 Updated LED
    [FruitMachineLED.fzz]
2021-08-05 Various updates to reels and lamps
    [FruitMachineReels.fzz]
2021-08-06 Coin Acceptor WIring
    [Coin Acceptor.fzz]
2021-08-06 Coin sensor
    [FruitMachineOptoSensors.fzz]
2021-08-07 VFD updates
    [VFD Displays.fzz]
2021-08-08 Added manuals and got BellFruit VFD working
    [VFD Displays.fzz]
2021-08-15 updated circuit diagrams
    [FruitMachine.fzz, VFD Displays.fzz]
2021-08-16 Cable Harness photos
2021-08-17 Various updates
    [FruitMachineReels.fzz]
2021-08-22 Combined Max-A-Million into single controller
    [FruitMachine.fzz]
2021-08-23 Updated Max-a-Million source
2021-09-01 Moved 7 Segment control to I2C daughterboard
2021-09-10 Updated game logic
    [FruitMachineLED_recovered.fzz]
2021-09-11 Separated out hold button relays
2021-09-16 updates for new board types
2021-09-17 Production version as at 17/09/21
    [VFD Displays.fzz]
2021-09-25 Update MaxAMillion.ino
    Added calibration loop to RC button 'D', and entered ready state immediately after setup() so the VFD correctly displays first character of message.
    [MaxAMillion.ino]
2022-03-10 Update MaxAMillion.ino
    Removed blocking delay and re-calibration that were causing jitters post win-state.
    [MaxAMillion.ino]
2022-03-10 Update MaxAMillion.ino
    Added force override on RC button C, corrected spelling of "Clued Up". investigated but not resolved issue where reels get nudged after successful solve)
    [MaxAMillion.ino]
